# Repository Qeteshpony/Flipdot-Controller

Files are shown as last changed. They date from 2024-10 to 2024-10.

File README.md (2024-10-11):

# Flipdot Controller



3D Render

[Documentation](https://qeteshpony.github.io/Flipdot-Controller)

Replacement controller for a Lawo Luminator Flipdot Display

(This was designed and built in 2022, I just never published the sources so here we go)

The project is based around a Raspberry Pi Zero W which replaces the microcontroller/EPROM combination from the original controller board. I reverse engineered the original board and used some of its components, the two transistor arrays, to control the lines of the display. The columns are driven by the original FP2800A drivers. 

The board is designed using KiCAD with production and assembly by JLCPCB in mind. All parts are selected to be available from JLCPCB at the time of writing and as many parts as possible are used from their basic library.

It is made to fit onto the screw holes for the original board with help of a little 3D-printed adapter that also holds a 18V power supply. 

The ATtiny is connected to the raspberry pi via I2C and controls the backlight of the display which I replaced with UV LED strips. 

### FlipDotControllerBackpanel
This folder contains the sources for a small board I mounted into the casing backpanel of the display to show state of the raspberry pi and have a way to shut it down through a button.

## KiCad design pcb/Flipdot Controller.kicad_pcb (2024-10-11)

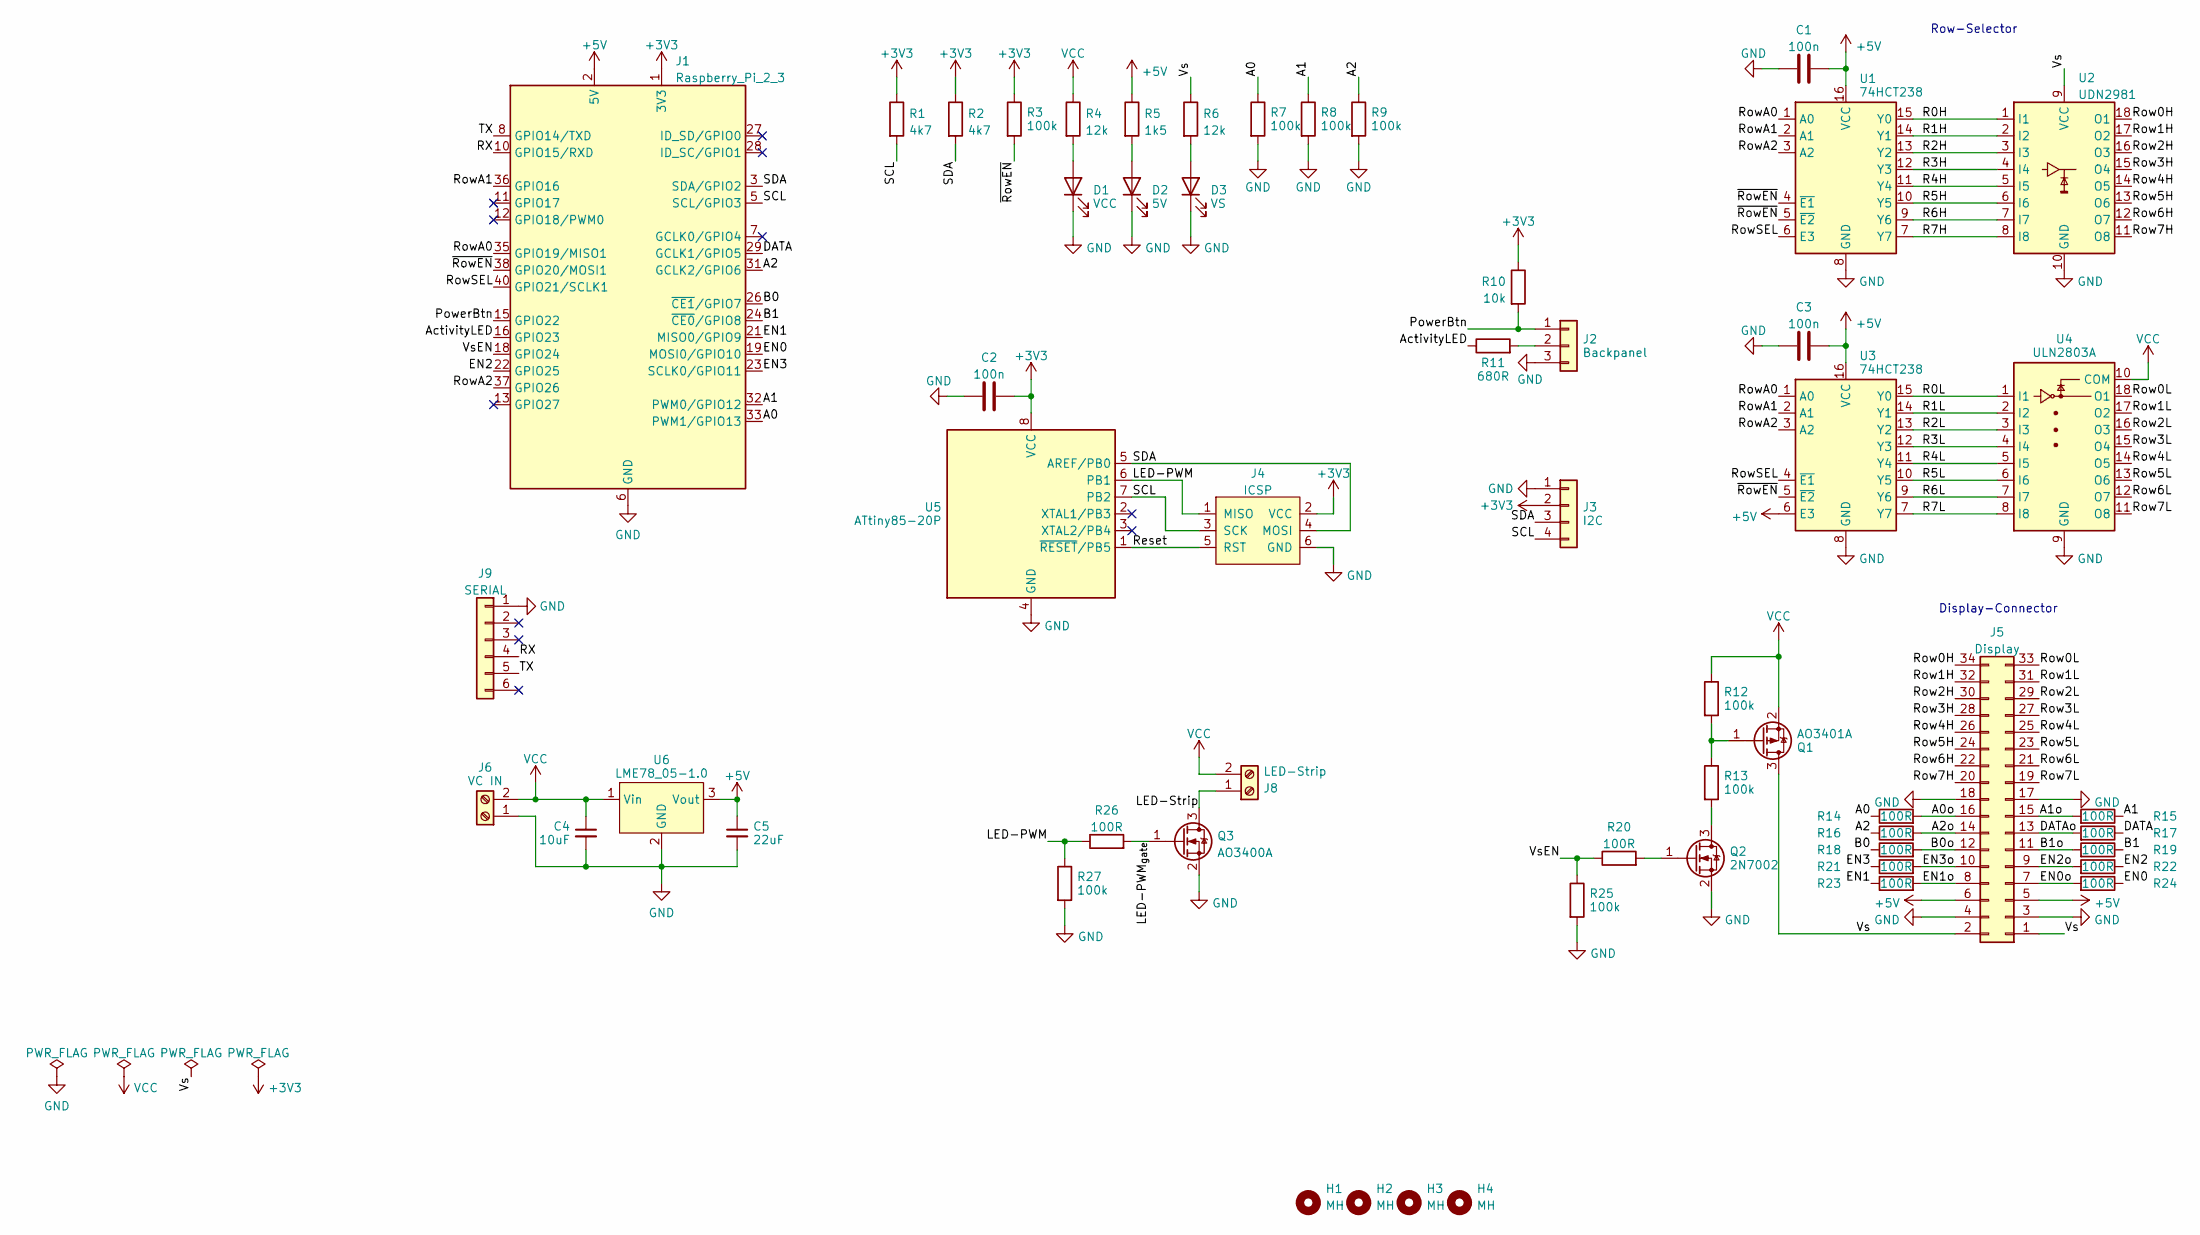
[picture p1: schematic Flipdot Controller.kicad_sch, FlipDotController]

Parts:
C1, C2, C3: 100n; C_0402_1005Metric; LCSC C307331
C4: 10uF; C_1206_3216Metric; LCSC C13585
C5: 22uF; C_0805_2012Metric; LCSC C45783
D1: VCC; LED_0603_1608Metric; LCSC C72038
D2: 5V; LED_0603_1608Metric; LCSC C72038
D3: VS; LED_0603_1608Metric; LCSC C72038
H1, H4: MH; MountingHole_3.2mm_M3_Pad_Via
H2, H3: MH; Half_MountingHole_3.2mm_M3_Pad_NPTH
J1: Raspberry_Pi_2_3; Raspberry_Pi_Zero_Socketed_THT_FaceDown_MountingHoles; LCSC C2977589
J2: Backpanel; JST_PH_B3B-PH-K_1x03_P2.00mm_Vertical; LCSC C5359600
J3: I2C; JST_PH_B4B-PH-K_1x04_P2.00mm_Vertical
J4: ICSP; PinHeader_2x03_P2.54mm_Vertical
J5: Display; IDC-Header_2x17_P2.54mm_Vertical
J6: VC IN; CTB9352-2
J8: LED-Strip; CTB9352-2
J9: SERIAL; PinSocket_1x06_P2.54mm_Vertical
Q1: AO3401A; SOT-23; LCSC C15127
Q2: 2N7002; SOT-23; LCSC C8545
Q3: AO3400A; SOT-23; LCSC C20917
R1, R2: 4k7; R_0402_1005Metric; LCSC C25900
R3, R7, R8, R9, R12, R13, R25, R27: 100k; R_0402_1005Metric; LCSC C25741
R4, R6: 12k; R_0603_1608Metric; LCSC C22790
R5: 1k5; R_0603_1608Metric; LCSC C22843
R10: 10k; R_0402_1005Metric; LCSC C25744
R11: 680R; R_0603_1608Metric; LCSC C23228
R14, R15, R16, R17, R18, R19, R20, R21, R22, R23, R24, R26: 100R; R_0402_1005Metric; LCSC C25076
U1, U3: 74HCT238; DIP-16_W7.62mm_Socket; LCSC C2874010
U2: UDN2981; DIP-18_W7.62mm_Socket; LCSC C2874011
U4: ULN2803A; DIP-18_W7.62mm_Socket; LCSC C2874011
U5: ATtiny85-20P; DIP-8_W7.62mm_Socket; LCSC C2874007
U6: LME78_05-1.0; LME78_1.0-Series

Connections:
+3V3: C2.2, J1.1 (3V3), J1.17 (3V3), J3.2, J4.2 (VCC), R1.1, R2.1, R3.1, R10.1, U5.8 (VCC)
+5V: C1.2, C3.2, C5.1, J1.2 (5V), J1.4 (5V), J5.5, J5.6, R5.1, U1.16 (VCC), U3.6 (E3), U3.16 (VCC), U6.3 (Vout)
/A0: J1.33 (PWM1/GPIO13), R7.1, R14.1
/A0o: J5.16, R14.2
/A1: J1.32 (PWM0/GPIO12), R8.1, R15.1
/A1o: J5.15, R15.2
/A2: J1.31 (GCLK2/GPIO6), R9.1, R16.1
/A2o: J5.14, R16.2
/ActivityLED: J1.16 (GPIO23), R11.1
/B0: J1.26 (~CE1/GPIO7), R18.1
/B0o: J5.12, R18.2
/B1: J1.24 (~CE0/GPIO8), R19.1
/B1o: J5.11, R19.2
/DATA: J1.29 (GCLK1/GPIO5), R17.1
/DATAo: J5.13, R17.2
/EN0: J1.19 (MOSI0/GPIO10), R24.1
/EN0o: J5.7, R24.2
/EN1: J1.21 (MISO0/GPIO9), R23.1
/EN1o: J5.8, R23.2
/EN2: J1.22 (GPIO25), R22.1
/EN2o: J5.9, R22.2
/EN3: J1.23 (SCLK0/GPIO11), R21.1
/EN3o: J5.10, R21.2
/LED-PWM: J4.1 (MISO), R26.1, R27.1, U5.6 (PB1)
/LED-PWM_{gate}: Q3.1 (G), R26.2
/LED-Strip: J8.1, Q3.3 (D)
/PowerBtn: J1.15 (GPIO22), J2.1, R10.2
/R0H: U1.15 (Y0), U2.1 (I1)
/R0L: U3.15 (Y0), U4.1 (I1)
/R1H: U1.14 (Y1), U2.2 (I2)
/R1L: U3.14 (Y1), U4.2 (I2)
/R2H: U1.13 (Y2), U2.3 (I3)
/R2L: U3.13 (Y2), U4.3 (I3)
/R3H: U1.12 (Y3), U2.4 (I4)
/R3L: U3.12 (Y3), U4.4 (I4)
/R4H: U1.11 (Y4), U2.5 (I5)
/R4L: U3.11 (Y4), U4.5 (I5)
/R5H: U1.10 (Y5), U2.6 (I6)
/R5L: U3.10 (Y5), U4.6 (I6)
/R6H: U1.9 (Y6), U2.7 (I7)
/R6L: U3.9 (Y6), U4.7 (I7)
/R7H: U1.7 (Y7), U2.8 (I8)
/R7L: U3.7 (Y7), U4.8 (I8)
/RX: J1.10 (GPIO15/RXD), J9.4
/Reset: J4.5 (RST), U5.1 (~RESET/PB5)
/Row0H: J5.34, U2.18 (O1)
/Row0L: J5.33, U4.18 (O1)
/Row1H: J5.32, U2.17 (O2)
/Row1L: J5.31, U4.17 (O2)
/Row2H: J5.30, U2.16 (O3)
/Row2L: J5.29, U4.16 (O3)
/Row3H: J5.28, U2.15 (O4)
/Row3L: J5.27, U4.15 (O4)
/Row4H: J5.26, U2.14 (O5)
/Row4L: J5.25, U4.14 (O5)
/Row5H: J5.24, U2.13 (O6)
/Row5L: J5.23, U4.13 (O6)
/Row6H: J5.22, U2.12 (O7)
/Row6L: J5.21, U4.12 (O7)
/Row7H: J5.20, U2.11 (O8)
/Row7L: J5.19, U4.11 (O8)
/RowA0: J1.35 (GPIO19/MISO1), U1.1 (A0), U3.1 (A0)
/RowA1: J1.36 (GPIO16), U1.2 (A1), U3.2 (A1)
/RowA2: J1.37 (GPIO26), U1.3 (A2), U3.3 (A2)
/RowSEL: J1.40 (GPIO21/SCLK1), U1.6 (E3), U3.4 (~E1)
/SCL: J1.5 (SCL/GPIO3), J3.4, J4.3 (SCK), R1.2, U5.7 (PB2)
/SDA: J1.3 (SDA/GPIO2), J3.3, J4.4 (MOSI), R2.2, U5.5 (AREF/PB0)
/TX: J1.8 (GPIO14/TXD), J9.5
/Vs: J5.1, J5.2, Q1.3 (D), R6.1, U2.9 (VCC)
/VsEN: J1.18 (GPIO24), R20.1, R25.1
/~RowEN: J1.38 (GPIO20/MOSI1), R3.2, U1.4 (~E1), U1.5 (~E2), U3.5 (~E2)
GND: C1.1, C2.1, C3.1, C4.2, C5.2, D1.1 (K), D2.1 (K), D3.1 (K), J1.6 (GND), J1.9 (GND), J1.14 (GND), J1.20 (GND), J1.25 (GND), J1.30 (GND), J1.34 (GND), J1.39 (GND), J2.3, J3.1, J4.6 (GND), J5.3, J5.4, J5.17, J5.18, J6.1, J9.1, Q2.2 (S), Q3.2 (S), R7.2, R8.2, R9.2, R25.2, R27.2, U1.8 (GND), U2.10 (GND), U3.8 (GND), U4.9 (GND), U5.4 (GND), U6.2 (GND)
unnamed: D1.2 (A), R4.2
unnamed: D2.2 (A), R5.2
unnamed: D3.2 (A), R6.2
unnamed: J2.2, R11.2
unnamed: Q1.1 (G), R12.2, R13.1
unnamed: Q2.3 (D), R13.2
unnamed: Q2.1 (G), R20.2
VCC: C4.1, J6.2, J8.2, Q1.2 (S), R4.1, R12.1, U4.10 (COM), U6.1 (Vin)

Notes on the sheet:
Row-Selector
Display-Connector

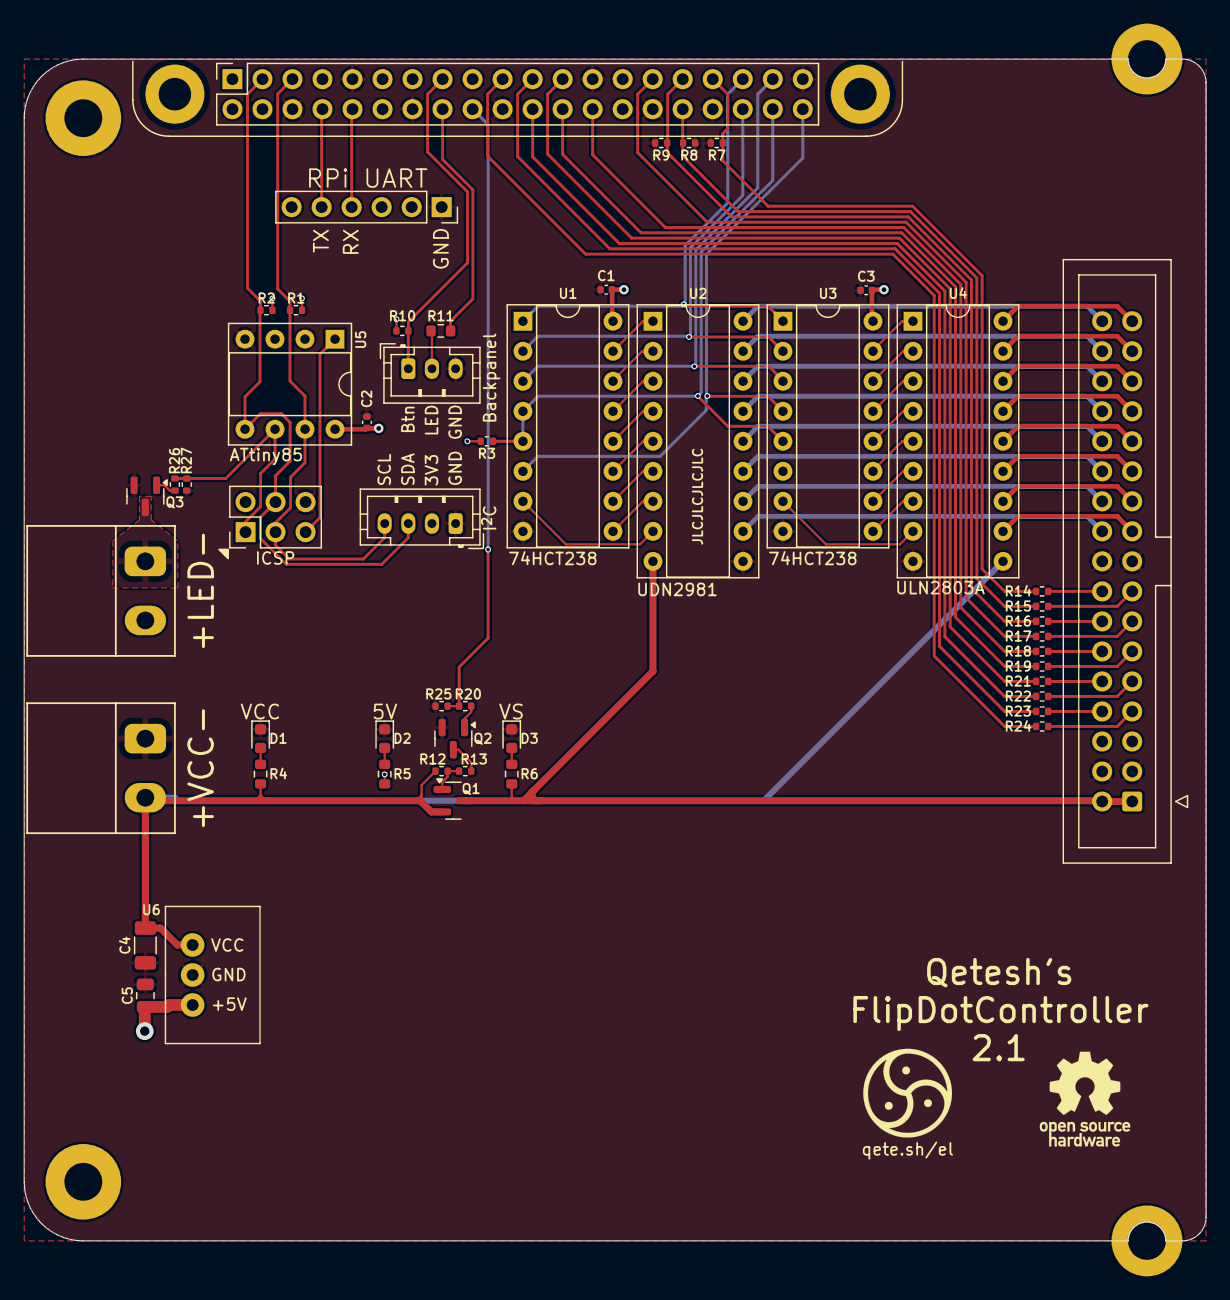
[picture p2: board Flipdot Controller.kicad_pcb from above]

Board: 2 copper layers, 100.0 x 100.0 mm, 56 parts (0 on the bottom side), 80 nets.

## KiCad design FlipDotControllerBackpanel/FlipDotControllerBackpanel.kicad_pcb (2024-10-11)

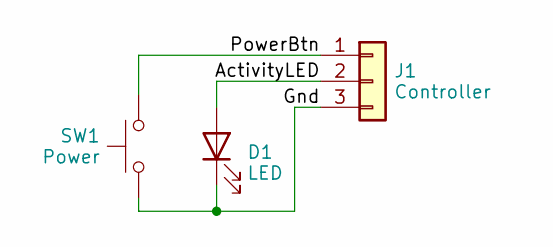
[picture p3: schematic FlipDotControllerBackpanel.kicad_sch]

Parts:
D1: LED; LED_D3.0mm
J1: Controller; JST_PH_B3B-PH-K_1x03_P2.00mm_Vertical; LCSC C5359600
SW1: Power; SW_PUSH_6mm_H4.3mm

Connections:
/ActivityLED: D1.2 (A), J1.2
/Gnd: D1.1 (K), J1.3, SW1.1
/PowerBtn: J1.1, SW1.2

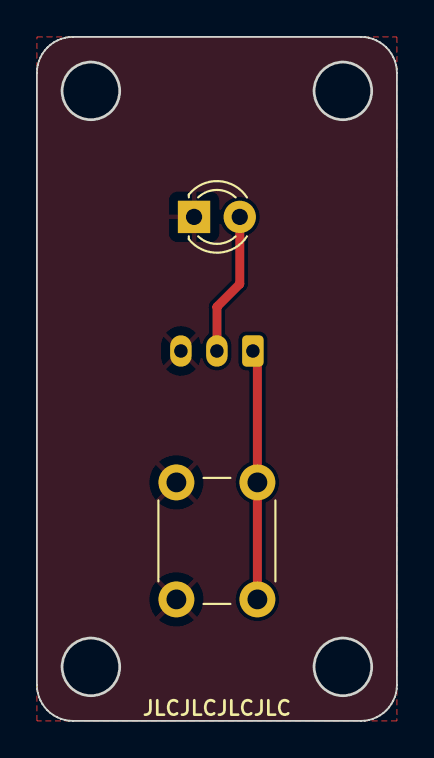
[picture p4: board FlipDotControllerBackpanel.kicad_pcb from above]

Board: 2 copper layers, 20.0 x 38.0 mm, 3 parts (1 on the bottom side), 3 nets.

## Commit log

2024-10-11 feat: initial upload
    [FlipDotControllerBackpanel.kicad_pcb, FlipDotControllerBackpanel.kicad_sch, Flipdot Controller.kicad_pcb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]
2024-10-11 docs: remove wrong model from 3d render
    [Flipdot Controller.kicad_pcb]
